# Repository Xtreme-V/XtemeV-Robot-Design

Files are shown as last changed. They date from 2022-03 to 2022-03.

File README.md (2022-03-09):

# XtemeV Robot
This robot was designed for the task given in **EN2532 - Robot Design and Competition** module in Semester 3 (2021), University of Moratuwa.

## Task
1. Line following
    - The robot must follow a white line on a black surface. These paths may contain straight
lines, curved lines, or dotted line segments.
2. Wall maze
    - After a line following section, the robot will have to navigate through a wall maze
section. This maze will not contain any looping paths. (A single possible path from
start to end is guaranteed.)
3. Mosaic Floor Area
    - The robot exiting the wall maze should immediately enter the mosaic floor area and
proceed to complete the following subtasks. Inserting the key solids to respective
keyholes to close the bridge. Collecting the ball of the color assigned to your team at
the start of the competition.
4. Bridge
    - The robot should cross the closed bridge and exit the area to a dotted line segment.
5. Shooting area
    - The robot must choose the correct path at the Y junction area according to the assigned color. While staying in the restricted space, the robot will have to shoot the
collected ball into the goal.
<br>
<p align="center">
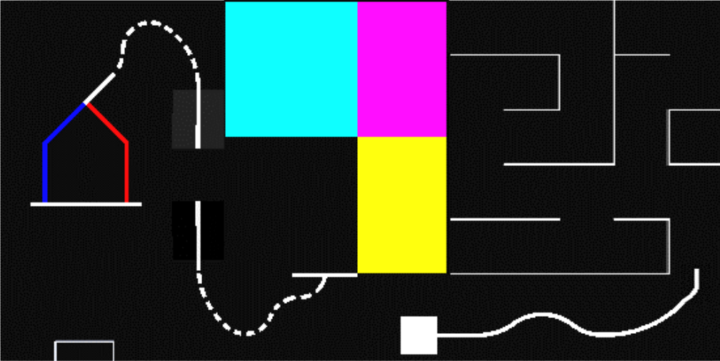
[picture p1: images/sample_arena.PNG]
    
</p>
<br>

## Robot Design
<br>
<p align="center">
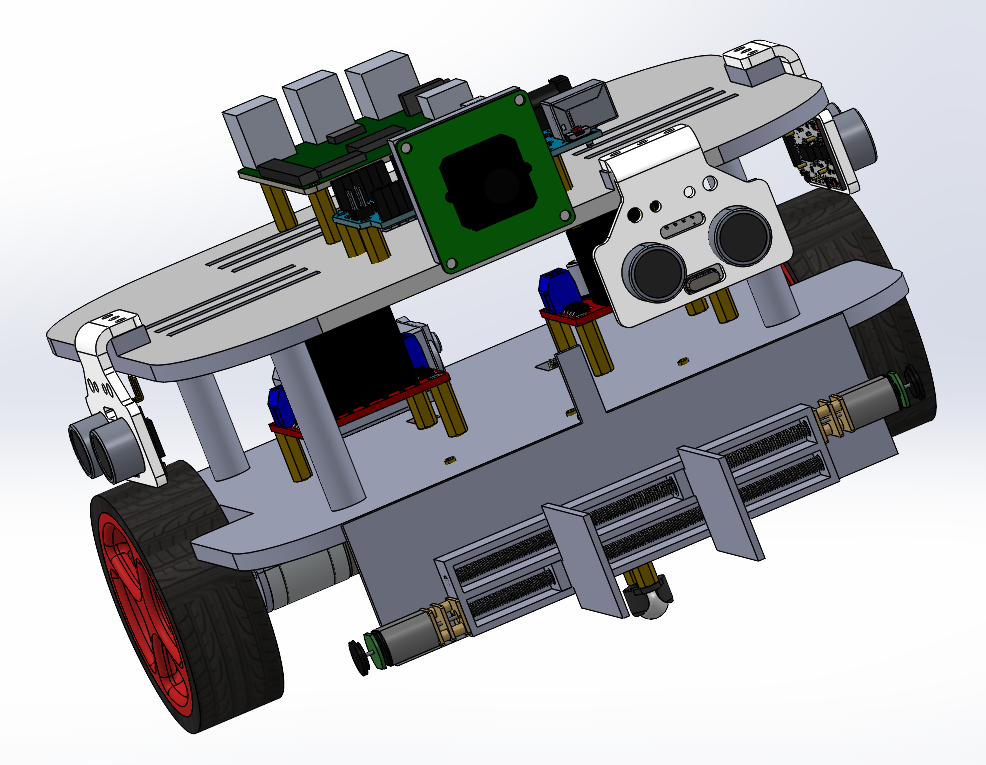
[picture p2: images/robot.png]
    
</p>
<br>

### Components that are being used in our robot are as follows,
- Pololu motors 
- N20 motors
- IR panel (QTR - 8RC)
- Ultrasonic Sensor (HC-SR04)
- Raspberry Pi Camera
- Raspberry Pi 3B+
- Arduino Mega
- Motor Controller (L298N)
## Team Members
- [K. D. Supun Dasantha Kuruppu](https://github.com/SupunDK)
- [W. M. Limalka Sadith](https://github.com/limalkasadith)
- [Sithuruwan Prathapasinghe](https://github.com/PrathapasingheSP99)
- [E. M. Dumindu Ashen Bandara](https://github.com/Dumindu-Bandara)
- [Biyon Fernando](https://github.com/BiyonFernando)

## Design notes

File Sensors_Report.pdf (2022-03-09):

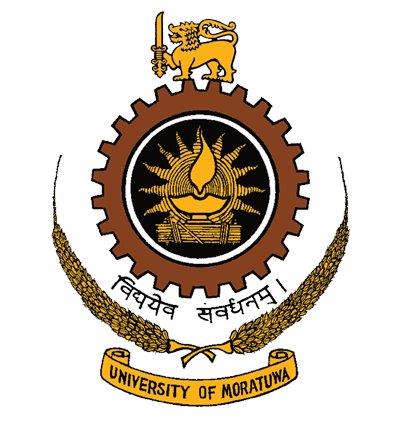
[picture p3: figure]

## Department of Electronic & Telecommunication Engineering

## University of Moratuwa

### Sensor Selection - XtremeV

14

## th October 2021

Bandara E. M. D. A. | 190072E
Fernando P. B. M. | 190178J
Kuruppu K. D. S. D. | 190338C
Prathapasinghe S. P. | 190470X
Sadith W. M. L. | 190538N

### 1. Motor Encoders

We are planning to use two types of motors in our robot. They are,

- DC Gear Motors
- Servo Motors

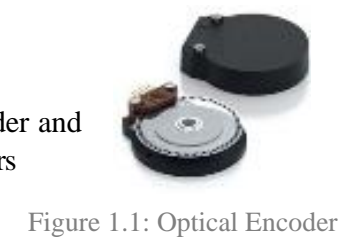
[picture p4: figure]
Figure 1.1: Optical Encoder

Since both the motors need to be controlled accurately, an optical quadrature encoder and an angle position tracking encoder is used in the DC Gear Motors and Servo Motors respectively.

Encoder for Servo Motor

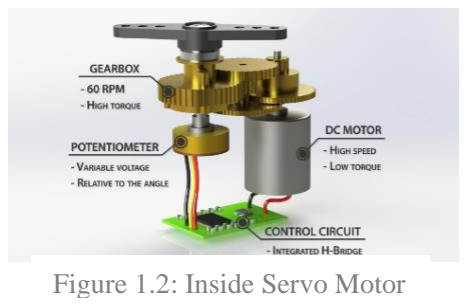
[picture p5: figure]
Figure 1.2: Inside Servo Motor

We are planning to use servo motors for the pick-and-place mechanism. It will require an angle position tracking encoder to control the angle of the servo motors. In the encoder market, we can purchase separate encoder modules which can connect to servo motors externally. The E3 optical kit encoder is an example for such an encoder. Since most of the servo motors have built-in potentiometer encoders, using such kind of servo motors for our robot is more economical. Therefore, we are planning to use Metal Wheel MG995 servo motors that have potentiometers as encoders.

Quadrature Encoder for Gear Motors

We chose the Pololu Gearmotor 25Dx64L which has a Hall effect Quadrature Encoder with a 1632 counts per revolution, as the wheel encoders for the DC Gear Motors. A high-resolution encoder was selected to achieve high controlling accuracy. The Quadrature Encoder is selected to fulfil the requirements for controlling the gear motors, which are to measure the rotational speed and the direction of the motor. The disadvantages of other encoder techniques are as follows,

Incremental Encoder (Not Quadrature) | It cannot measure the rotational direction of the motor
Absolute Encoder | The additional feature of precisely measuring the rotated angle is not required for our application

Even though optical encoders offer higher accuracy compared to magnetic
encoders in clean, and quiet environments, their performance significantly drop in environments with oil, dirt, and moisture. Similarly, their performance is affected by shock and vibration as well. On the contrary, the Hall effect encoders copes very well with shock and vibration while being unaffected by the ingress of oil, dirt, and moisture. Moreover, the hall effect encoders are compact and cost-effective, which makes them ideal for our application.

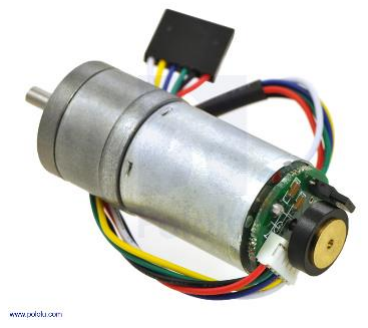
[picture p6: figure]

Figure 1.3: Pololu Gear motor

### 2. Distance Sensor

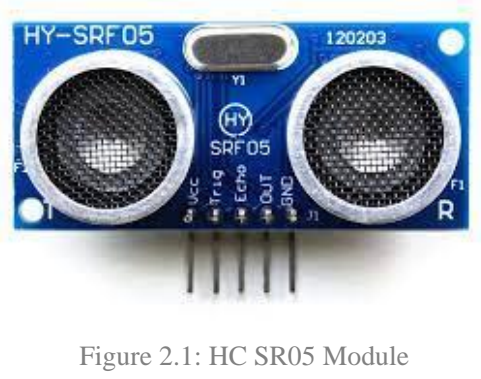
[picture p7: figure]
Figure 2.1: HC SR05 Module

HC-SR05 ultrasonic sensor has been chosen as the distance sensor for the maze navigation task in our robot. Three sensors are mounted on top of the robot to identify the obstacles around it. Ultrasonic sensors use the concept of time of flight to calculate the distance to an obstacle. It measures the time between transmitted and received signal and calculate distance using speed of sound in the air. There are two popular sensors in the ultrasonic sensor category. The HC-SR05 has been chosen over HC-SR04 due to its higher precision and the availability of the 3-pin mode operation. HC-SR05 sensor equipped with five pins, one each for VCC, Trigger, Echo, Out and Ground. It has a measurement range of 2cm to 450cm. One drawback of ultrasonic sensor is that its transmitted signals get distorted around complex objects.

Following is a comparison between alternatives available for ultrasonic sensors.

Ultrasonic | Sharp-IR | LIDAR | VCSEL
Low range | Low range | High range | Low range
Low frequency data retrieval | Low frequency data retrieval | High frequency data retrieval | High frequency data retrieval
Less Cost | Moderate Cost | High Cost | High Cost
Multiple interface options | Analog output | UART/ I2C | I2C interface only
Low resolution | High resolution | High resolution | High resolution

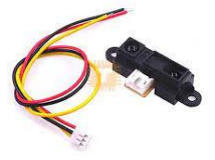
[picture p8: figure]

### 3. IR Sensor Array

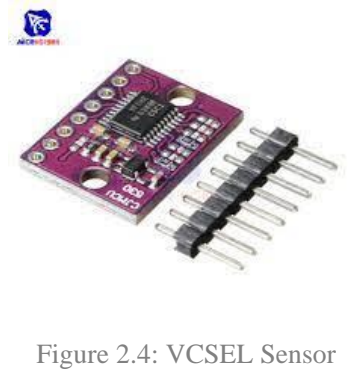
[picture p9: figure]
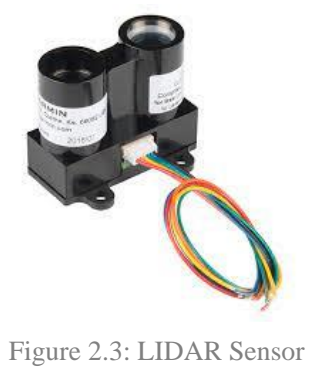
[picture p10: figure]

In this device, there are several IR sensors connected in series. There can be 5 sensors, 7 sensors or 8 sensors. This device used for the line following task. It’s easy to place and drive the robot in the middle of the line with this array.

Suitable IR Sensor arrays for the project are,

Figure 2.2: Sharp IR | Figure 2.3: LIDAR Sensor | Figure 2.4: VCSEL Sensor

Table 2.1: Comparison between distance sensors

1. Pololu QTR 8-bit Line Hunter Sensor Array Module for Arduino (MD0601) This IR array has 8 TCRT5000 IR sensors. It is a good sensor for line-following robots. It is very precise and easy to handle as well. The sensor outputs are digital I/O-compatible signals that can be read as a timed high
pulse. Moreover, there are LEDs for each sensor for indication. Operating voltage: - 3.3V - 5V Operating current: - 100mA Price: - Rs.2950.00

### 2. Reflective Sensor Array Raykha S8

This is the local version of the above sensor array. It is made in Sri Lanka, and it is as good as Pololu IR sensors but not that expensive. Each IR sensor has its own Digital I/O measurable output, variable analogue voltage output and an LED for indication purposes.
Supply Voltage: - 5V
Supply current: - max 200mA Price: - Rs.1290.00

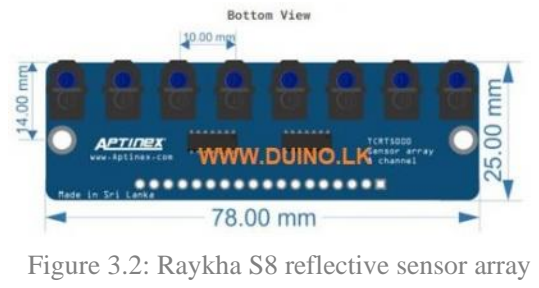
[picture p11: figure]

Comparison between Pololu and Rekha IR sensor arrays are as follows,

Pololu IR array | Rekha IR array
Expensive | Cheaper than Pololu
Have a built-in library | Don’t have built-in libraries

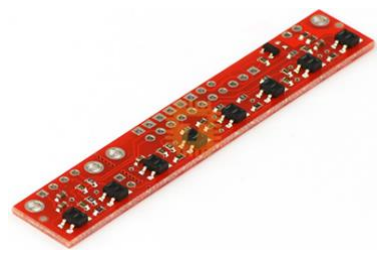
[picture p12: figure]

More precise values | Accuracy is a bit lower than Pololu
Both can give digital as well as analog outputs

### 4. IR Array or Camera

We are planning to use the camera for colour detection, object detection and obstacle detection. We have an idea to use the same camera module to accomplish the line following task as well. However, since we are unsure about the suitability of that approach, we are planning to experiment and decide. If it works, we won’t need an IR array for the line following task. Therefore, it would decrease the budget of the project.

Camera Module Selection

We planned to do following tasks using the Raspberry Pi camera,

1. Dotted Line Following
2. Object Detection
3. Colour Detection

Available Camera modules

### 1. Raspberry Pi Camera V2.1 (Original) (8MP)

Capture Resolution: 1080p
Special Feature: Time Lapse Price: Rs.6250.00

Figure 3.1: Pololu QTR IR Module

Figure 3.2: Raykha S8 reflective sensor array

Figure 4.1: Raspberry Pi Camera V2.1

Figure 4.2: Banana Pi Camera Module

Table 3.1: Comparison between Pololu and Rekha IR sensor arrays

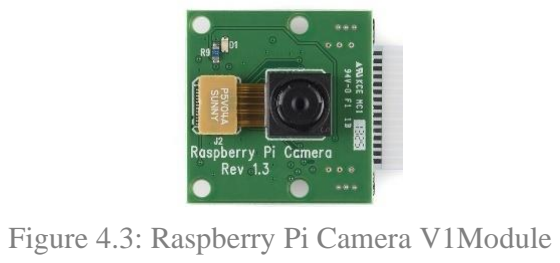
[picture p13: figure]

### 2. Banana Pi Camera Module (5MP)

Capture Resolution: 1080p
Price: Rs.5500.00

### 3. Raspberry Pi Camera V1 (5MP)

Capture Resolution: 1080p
Price: Rs.1490.00

### 4. Raspberry Pi NoIR Camera Module V2 (8MP)

Official Night vision camera for RPi Capture Resolution: 1080p
Special Feature: Time Lapse, Night Vision Price: Rs.7250.00

We decided to use Raspberry Pi Camera V1 (5MP) module because its cost effective and capable of performing all the desired tasks. Since we are planning to use the Raspberry Pi camera in multiple occasions, native compatibility with the Raspberry Pi board is a huge advantage and it would allow efficient use of board’s resources. Furthermore, the availability of this camera module in the local market (Tronic.lk) is another advantage.

### 5. References

1. https://www.seeedstudio.com/blog/2020/05/14/raspberry-pi-camera-comparison-of-high-quality-camera-with-camera-module-v2/ (https://www.seeedstudio.com/blog/2020/05/14/raspberry-pi-camera-comparison-of-high-quality-camera-with-camera-module-v2/)
2. https://tronic.lk/product/banana-pi-camera-module
3. https://tronic.lk/product/raspberry-pi-noir-camera-v2-sony-imx219-sensor-8-megapi
4. https://tronic.lk/product/raspberry-pi-camera-v2-1-sony-imx219-sensor-8-megapixel
5. https://www.amazon.com/Raspberry-Pi-Camera-Module-Megapixel/dp/B01ER2SKFS
6. https://maker.pro/raspberry-pi/projects/raspberry-pi-webcam-robot
7. https://forums.raspberrypi.com/viewtopic.php?t=42169
8. https://www.sparkfun.com/distance_sensor_comparison_guide
9. https://www.seeedstudio.com/blog/2019/12/23/distance-sensors-types-and-selection-guide/

Figure 4.3: Raspberry Pi Camera V1Module

Figure 4.3 Raspberry Pi NoIR Camera Module

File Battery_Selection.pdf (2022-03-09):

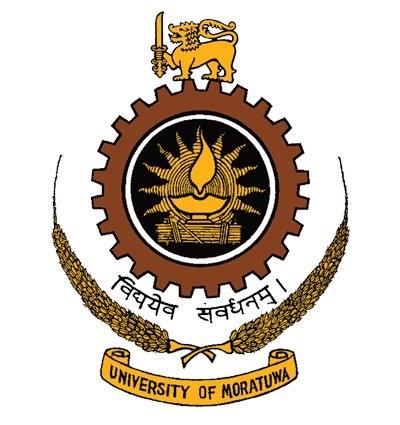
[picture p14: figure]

### Department of Electronic & Telecommunication Engineering

### University of Moratuwa

Assignment – 8

EN2532 - Robot Design and Competition

Bandara E. M. D. A. | 190072E
Fernando P. B. M. | 190178J
Kuruppu K. D. S. D. | 190338C
Prathapasinghe S. P. | 190470X
Sadith W. M. L. | 190538N

### 19th November 2021

Power Budget Calculation

The current and voltage requirements of the components that are being used in our robot are as follows,

Component | Quantity | Voltage | Operating Current | Maximum Current
Pololu motor | 2 | 6 V | 2.06 A (1.03 A x 2) | 5.6 A (2.8 A x 2)
N20 motor | 2 | 6 V | 2 A (1 A x 2) | 3 A (1.5 A x 2)
IR panel | 1 | 5 V | 100 mA | 100 mA
Ultrasonic Sensor | 3 | 5 V | 45 mA (15 mA x 3) | 45 mA (15 mA x 3)
Raspberry Pi 3B+ | 1 | 5 V | 3 A | 3 A
Solenoid | 1 | 12 V | 350 mA | 350 mA
Arduino Uno | 1 | 5 V | 200 mA | 200 mA
Motor Controller | 2 | 5 V | 80 mA (40 mA x 2) | 80 mA (40 mA x 2)
Total | | | 7.835 A | 12.375 A

Voltage

The component that requires the maximum voltage in the component list is the Solenoid. It requires 12 V, and all the other components require 6 V or less. Furthermore, the Solenoid only requires 350 mA which is relatively low. Therefore, we decided to use a boost converter along with a 11.1 V battery for our robot.

Capacity

The maximum current draw and the operating current draw of the robot are 12.375 A and 7.835 A respectively. Since the maximum current draw only occurs when the DC motors are in the stall condition, considering a continuous current draw of 12.375 A is not realistic. Therefore, the capacity requirement for the robot is based on the operating current. Furthermore, we decided that a 20-minute continuous run-time for the robot is sufficient for our application. Therefore, the required capacity of the power source is calculated as follows,

Capacity = CurrentDraw(mA) ∗ Time(ℎours)

Capacity = 7835 ∗ (

20
60)

Capacity = 2611 mAℎ

Discharging Rate

The capacity of the required battery is 2611 mAh. The operating current of the robot is 7.835
A. Therefore, the required discharging rate should be greater than,

Discℎaring Rate =

7835
2611

Discℎaring Rate = 3 C

The summarised requirements of the power source are as follows,

Voltage | Capacity | Discharging Rate
11.1 V | 2611 mAh | 3C or above

Battery Selection

The NiCd battery is not considered as a viable battery option due to the toxic nature of the battery and the memory effect associated with its rechargeability.

The Lead Acid battery is also not considered as a viable battery option, since it is considerably heavy, and it is not suitable for a compact mobile robot as ours.

| Alkaline | NiMH | LiPo | Li-ion
Capacity | Low | High | High | High
Discharging Rate | Low | Low | High | Low
Power Density | Low | Moderate | High | High
Rechargeability | Not Available | Available | Available | Available

Since we require a rechargeable battery with high capacity and discharging rate, we identified the LiPo battery as the most suitable based on the above comparison table.

The following LiPo battery in the market fulfils all the identified requirements.

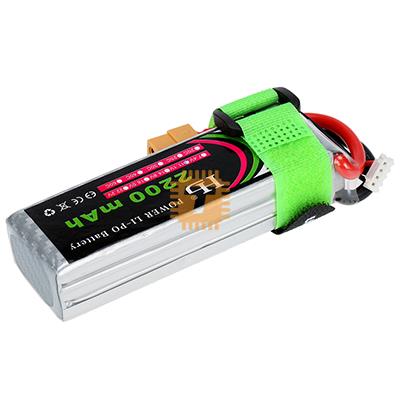
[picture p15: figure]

https://tronic.lk/product/11-1v-2200mah-3s-25c-lipo-battery-xt60-plug

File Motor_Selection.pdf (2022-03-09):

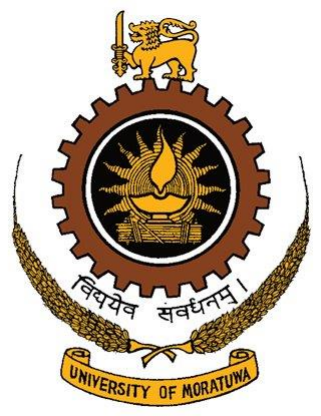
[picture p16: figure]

### Department of Electronic & Telecommunication Engineering

### University of Moratuwa

Assignment – 5

EN2532 - Robot Design and Competition

27

### th October 2021

Bandara E. M. D. A. | 190072E
Fernando P. B. M. | 190178J
Kuruppu K. D. S. D. | 190338C
Prathapasinghe S. P. | 190470X
Sadith W. M. L. | 190538N

Robot Weight Calculation

The list of chosen components that add a significant weight to the robot are as follows,

- Battery: 250 g
- Raspberry-Pi 3B+ with clear case: 64 g
- MG995 Servo Motor (x2): 110 g
- Gripper: 100 g
- Robot Chassis with wheels: 330 g
- Motor Driver: 26 g
- Motor (x2): 202 g
- Caster Wheel (x2): 80 g

Therefore, the total weight of the robot accounts to,

Total weight = 1162 g

Requirements

1. Qualitative Requirements
- Since this robot is made for the EN2532 module, we only require the robot to last for six months.
- The motor should be affordable to align with the budget of the project.
- Medium level of accuracy is sufficient for the application.
2. Quantitative Requirements
- The distance the robot needs to traverse was estimated to be 20 m. We intend to complete the task within 5 minutes. Therefore, we chose the maximum velocity of the robot as 11 cms

-1
- The motors need to be able to provide enough torque to propel a weight of 1119 g on a 20° slope.
- The motor should run at 30% of its stall torque to operate with low current draw to ensure minimize losses.

Considering the above qualitative requirements, the Brushed DC motor seems the most suitable motor type for our application. Therefore, the following calculations are done in order to determine the quantitative requirements for the Brushed DC motors.

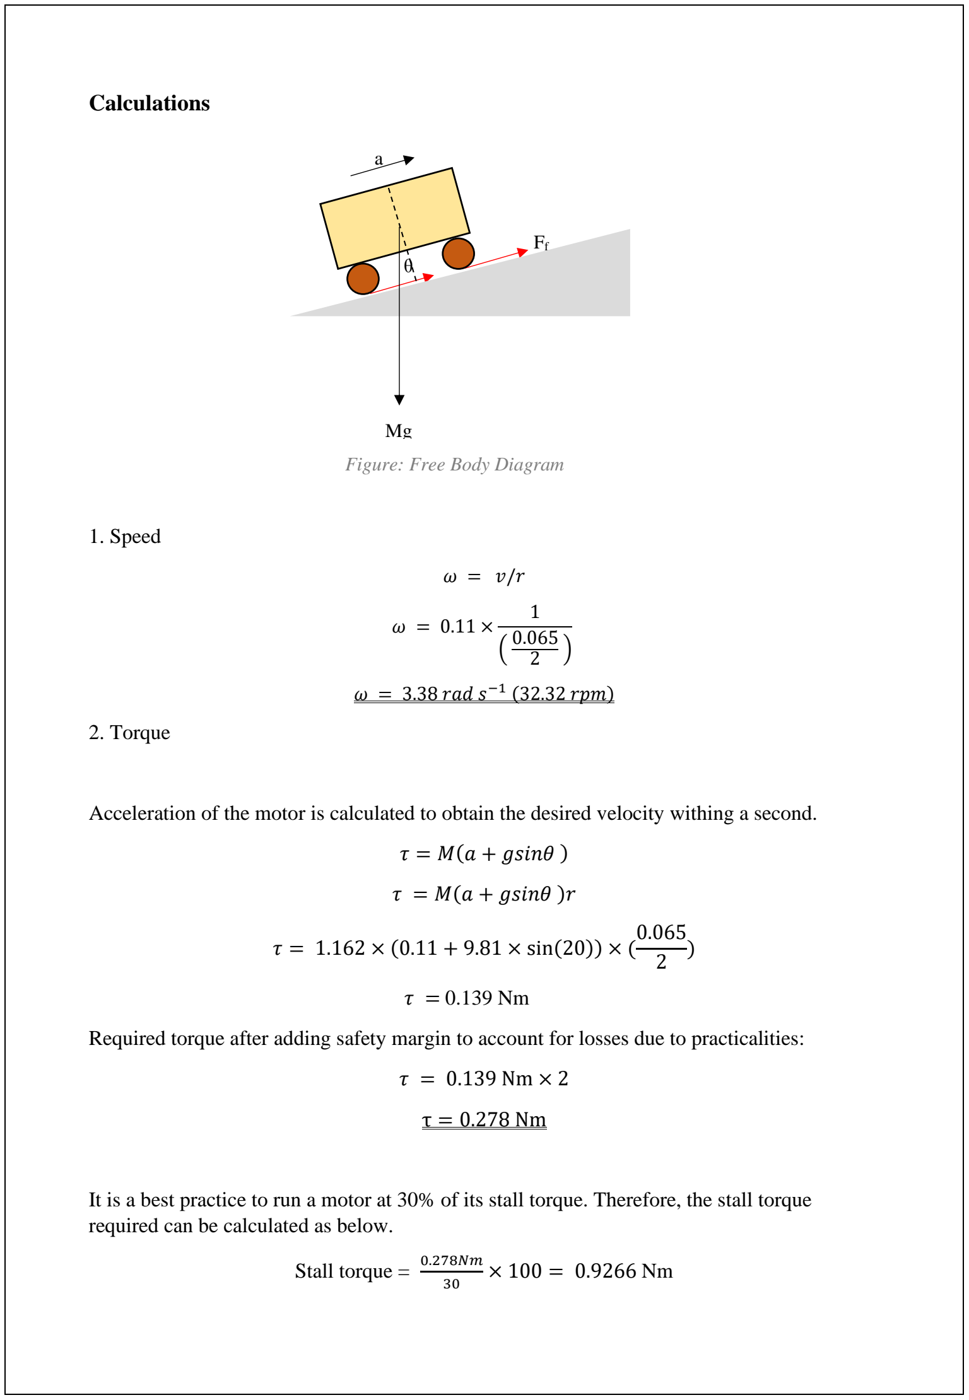
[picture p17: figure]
Calculations; 1. Speed; ω = 3.38 rad s; (32.32 rpm); 2. Torque; τ = M(a + gsinθ ); τ = M(a + gsinθ )r; τ = 1.162 × (0.11 + 9.81 × sin(20)) × (; required can be calculated as below.; Stall torque =; Figure: Free Body Diagram

Acceleration of the motor is calculated to obtain the desired velocity withing a second.

Required torque after adding safety margin to account for losses due to practicalities:

It is a best practice to run a motor at 30% of its stall torque. Therefore, the stall torque

Required Specifications for the DC motor

Motor type | Brushed DC Motor
Operational toque | 0.278 Nm (39.368 oz.in)
Operational speed | 3.38 rad s⁻¹ (32.32 rpm)
Stall torque | 0.9266Nm (131.22 oz.in)

Specifications of suitable DC motors

34:1 Metal Gearmotor 25Dx64L mm HP 12V with 48 CPR Encoder (No End Cap)
No Load RPM | 290 rpm
Stall torque | 120 oz-in

The above motor has a stall torque of 120 oz-in which is close to the required value of 131.22 oz-in. Furthermore, the No Load RPM is 290 rpm. Therefore, this motor aligns with all the boundary requirements.

According to the torque speed graph, we can calculate the operational speed at our required torque.

Operational speed = (

290
120

) × (120 − 39.368 ) = 194.86 rpm

The above calculation indicate that the motor can accommodate the required operational speed at the operational torque.

34:1 Metal Gearmotor 25Dx52L mm HP 12V
No Load RPM | 300 rpm
Stall torque | 150 oz-in

The above motor has a stall torque of 150 oz-in which is greater than 120 oz-in. The No Load RPM of the motor is 300 rpm which can easily accommodate our requirements.

According to the torque speed graph, we can calculate the operational speed at our required torque.

Operational speed = (

300
150) × (150 − 39.368 ) = 221.26 rpm

The above calculation indicate that the motor can accommodate the required operational speed at the operational torque.

Conclusion

After considering the above calculations and the qualitative requirements, we have selected 34:1 Metal Gearmotor 25Dx64L mm HP 12V with 48 CPR Encoder (No End Cap) as it is both suitable for our application and provided by the university.

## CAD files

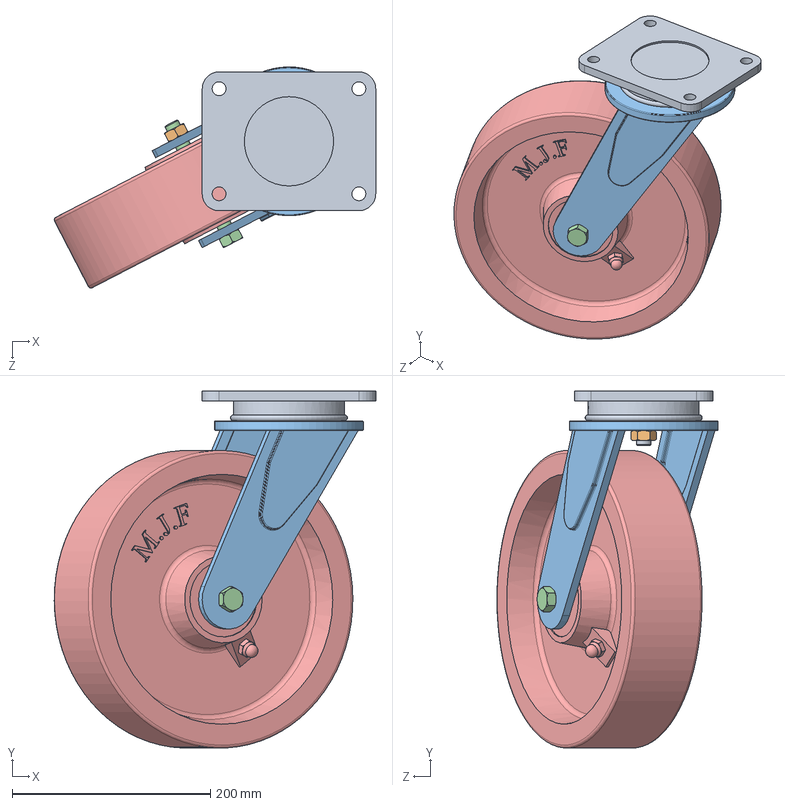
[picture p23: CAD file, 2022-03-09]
3D Design/Other parts/assembly of caster wheel.SLDASM
324.2 x 359.9 x 223.0 mm
part 1 mounting plate
part 2 nut x 2
part 3 horn
part 4 bolt
part 5 wheel

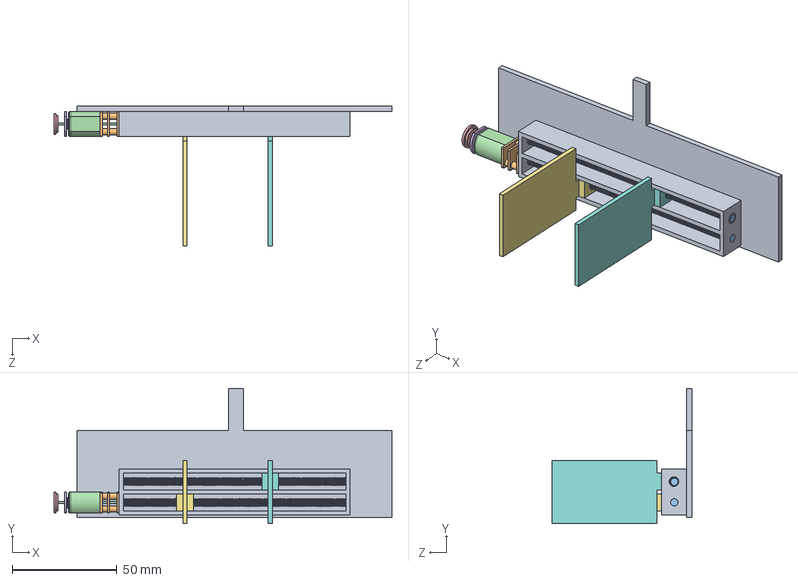
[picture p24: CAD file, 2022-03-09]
3D Design/gripper/Assem1.SLDASM
161.0 x 64.4 x 66.5 mm
rail
threaded rod.step x 4
handleft
handrigt

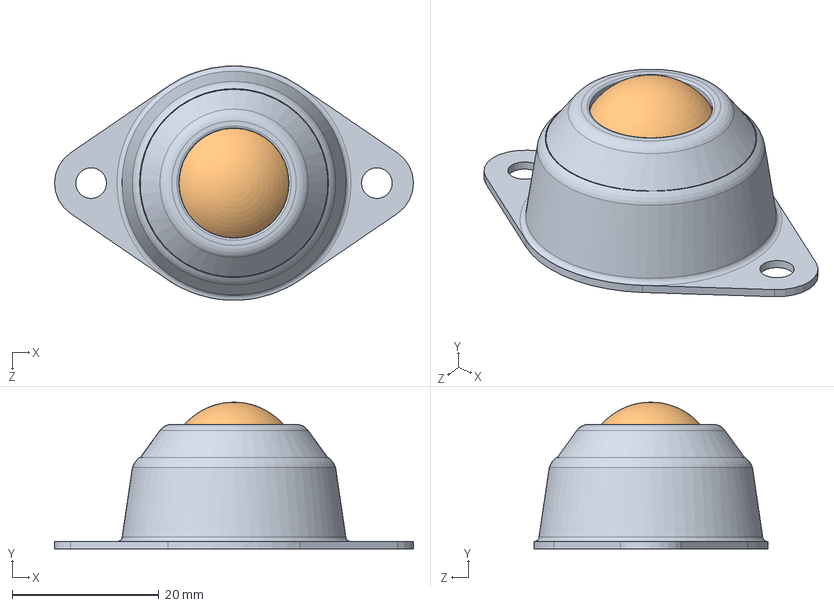
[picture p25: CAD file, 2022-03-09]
3D Design/Other parts/3/Omni wheel steel ball OW007.SLDASM
49.0 x 20.0 x 32.0 mm
Base
Balle
Fond

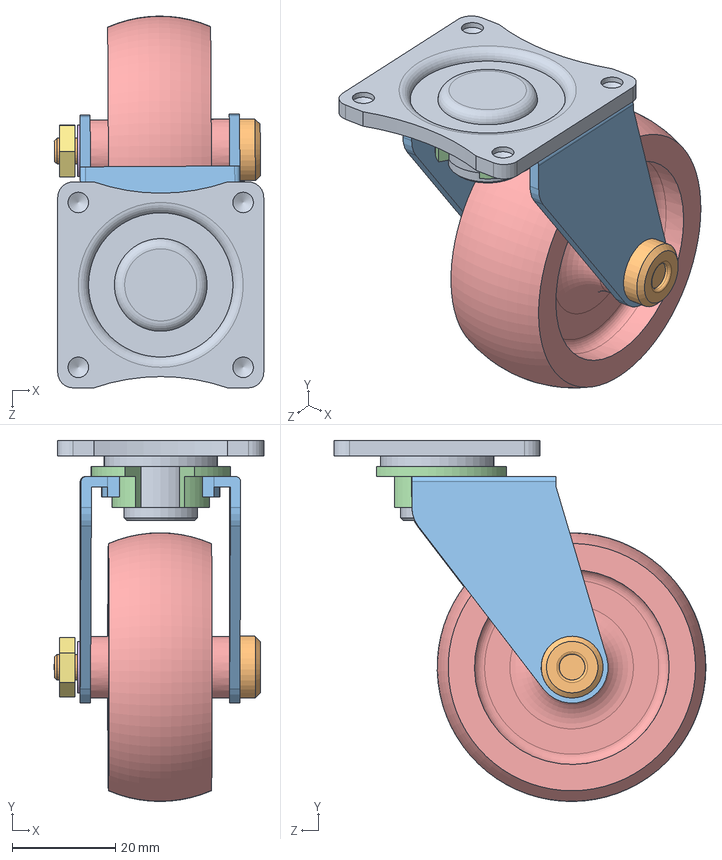
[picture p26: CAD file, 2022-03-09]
3D Design/Other parts/Castor Wheel Assembly.SLDASM
40.7 x 70.1 x 72.2 mm
Top
Holder
HOLDER 2
bottom
Wheel
washer
Nut

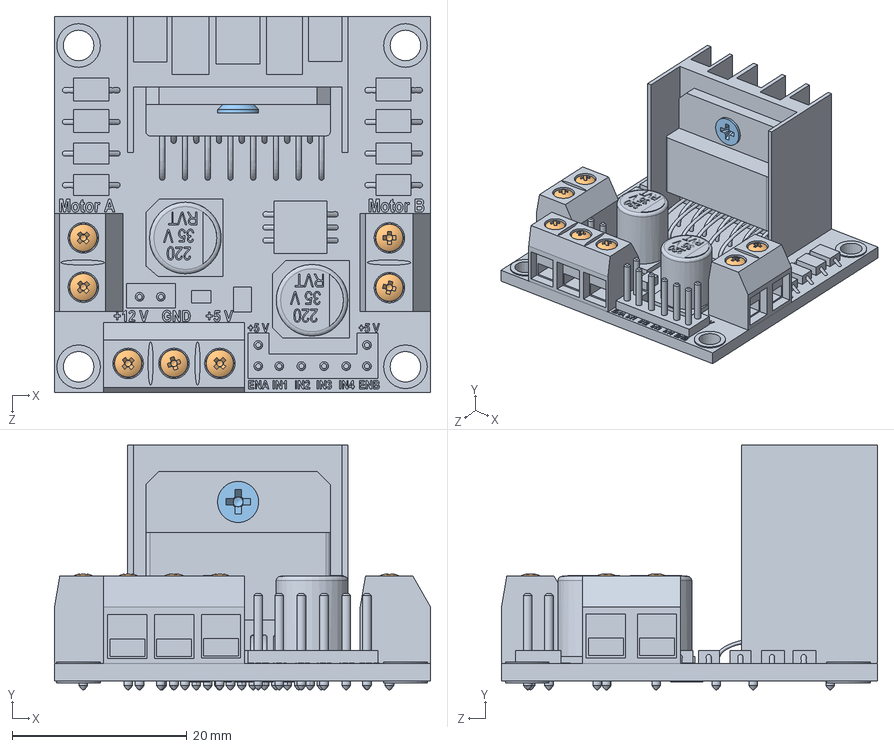
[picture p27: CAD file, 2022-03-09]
3D Design/Other parts/L298N Stepper Motor Driver Assembly.SLDASM
43.0 x 28.0 x 43.0 mm
L298N Stepper Motor Driver (Red)-Part File
pan head cross recess screw_iso_ISO 7045 - M1.6 x 4 - Z - 4N x 7
countersunk flat head cross recess screw_iso_ISO 7046-1 - M2.5 x 3 - Z - 3N

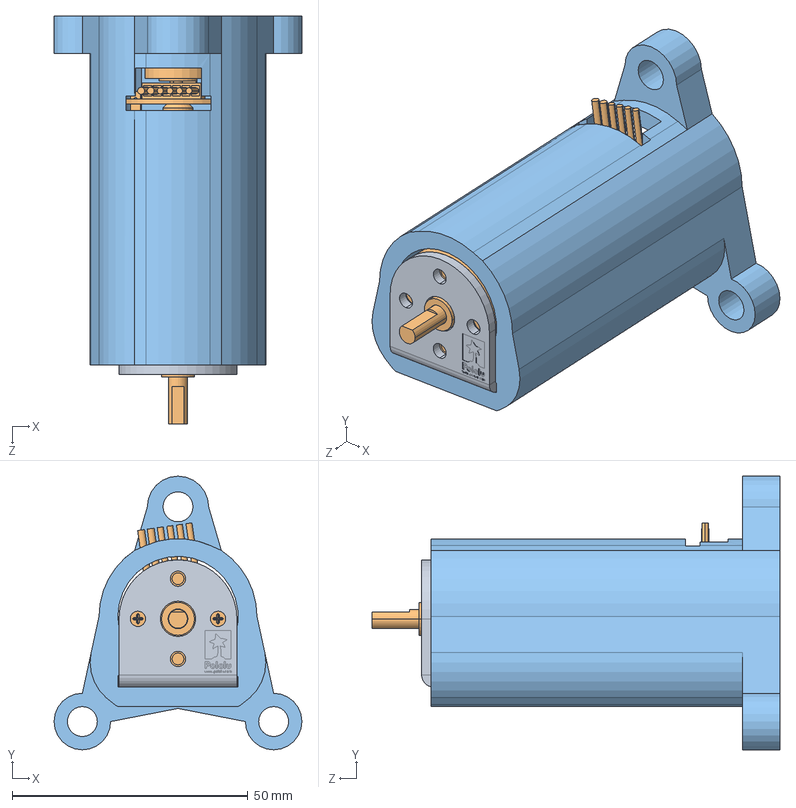
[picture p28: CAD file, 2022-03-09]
3D Design/Other parts/MotorenSoporte.SLDASM
52.6 x 58.0 x 86.5 mm
pololu-25d-mm-metal-gearmotor-bracket
25D-metal-gearmotor-75-encoder
SoporteMotor

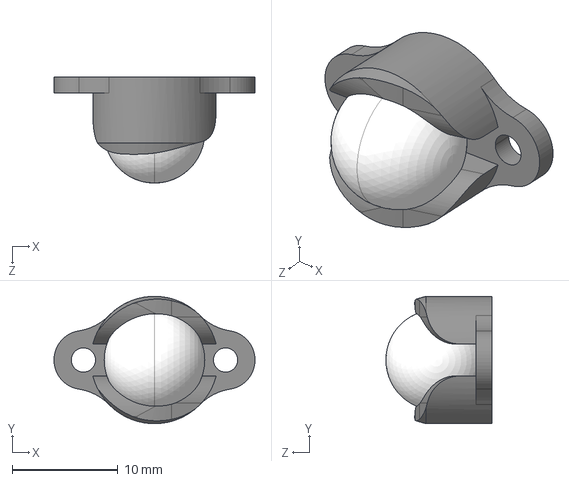
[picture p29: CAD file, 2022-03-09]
3D Design/gripper/casterwheel/pololu-ball-caster-with-0-375in-ball.step
19.0 x 12.1 x 10.1 mm

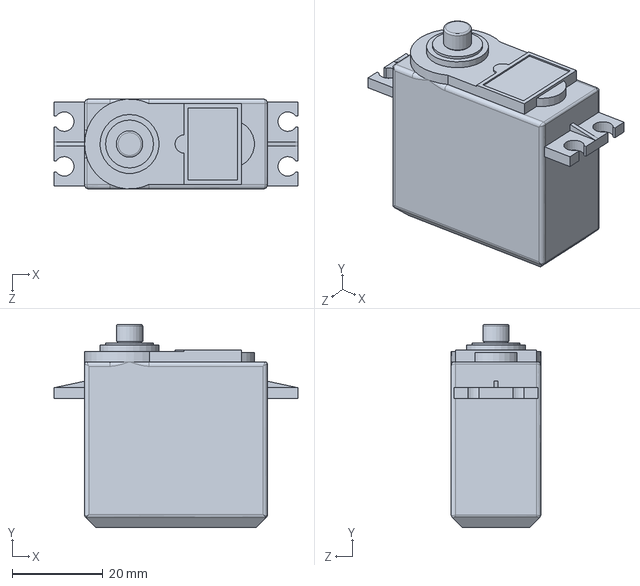
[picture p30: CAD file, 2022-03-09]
3D Design/gripper/kiso.SLDPRT
53.8 x 44.8 x 19.8 mm

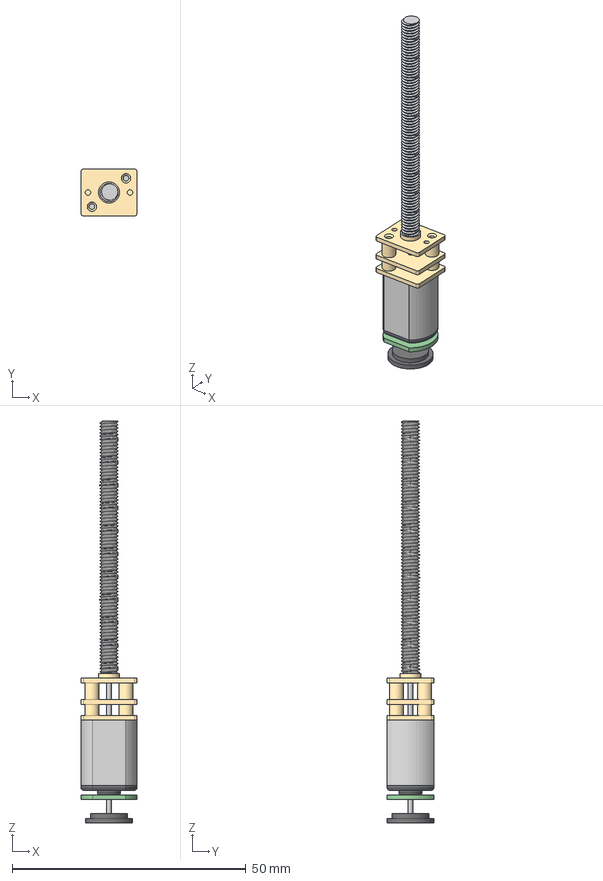
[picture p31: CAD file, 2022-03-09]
3D Design/gripper/motor/n20 m4x55 encoder v2.step
12.0 x 10.0 x 86.0 mm
gearbox
threaded rod
n20 motor
magnet
encoder

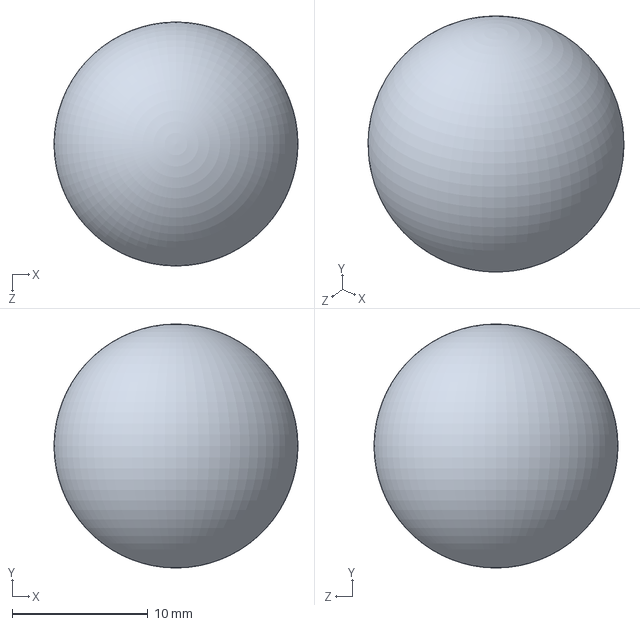
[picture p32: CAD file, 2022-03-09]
3D Design/Other parts/3/Balle.SLDPRT
18.0 x 18.0 x 18.0 mm

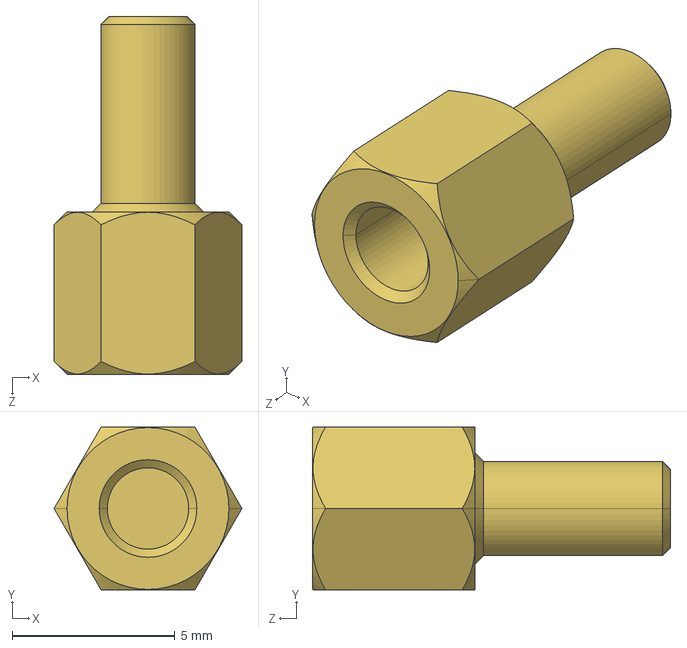
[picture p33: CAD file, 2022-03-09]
3D Design/Other parts/m3-standoff-pcb-spacers-1.snapshot.2/M3_M_TO_F_5MM_STANDOFF.STEP
5.77 x 5.00 x 11.0 mm

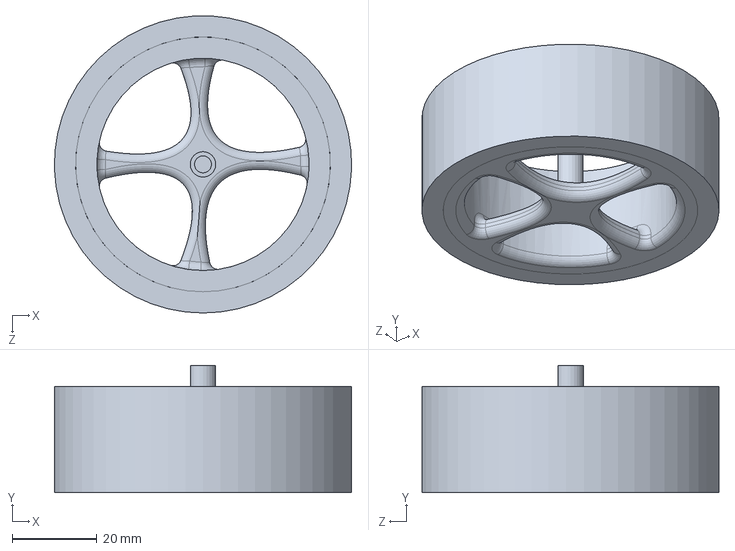
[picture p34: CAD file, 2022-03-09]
3D Design/Other parts/wheel - 1/wheel.SLDPRT
70.0 x 30.0 x 69.9 mm

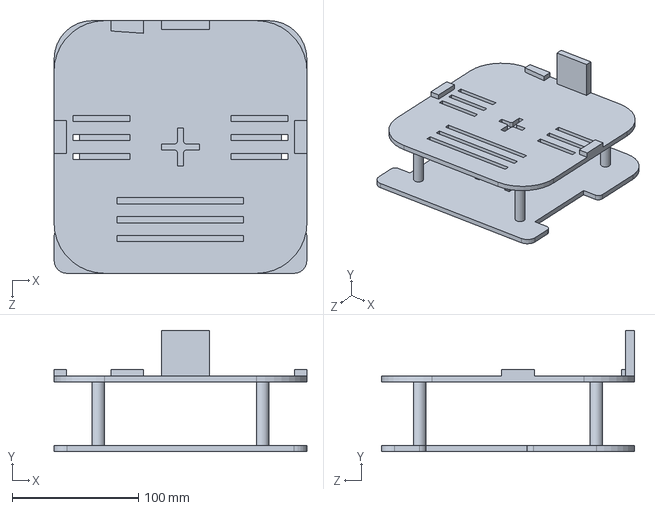
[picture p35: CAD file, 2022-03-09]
3D Design/robot chassis.SLDPRT
200.3 x 96.0 x 200.0 mm

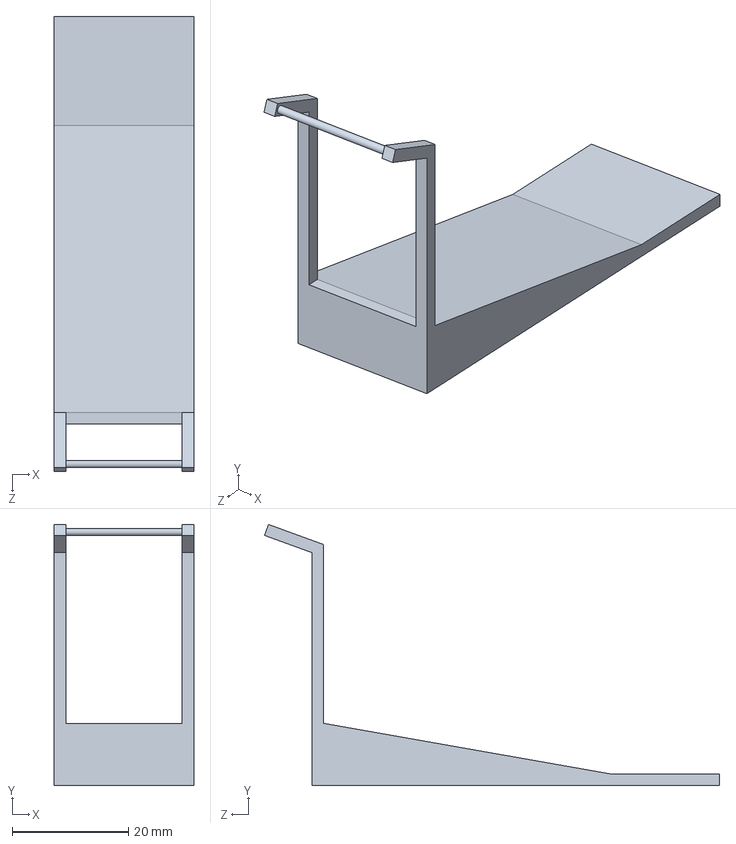
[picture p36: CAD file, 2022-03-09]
3D Design/solenoid/connector.SLDPRT
24.0 x 44.9 x 78.2 mm

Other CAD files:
3D Design/gripper/hand.SLDPRT
3D Design/Other parts/25D-metal-gearmotor-75-encoder.SLDPRT
3D Design/Other parts/3/Fond.SLDPRT
3D Design/Other parts/m3-standoff-pcb-spacers-1.snapshot.2/M3_F_TO_F_10MM_STANDOFF.STEP
3D Design/Other parts/3/Base.SLDPRT
3D Design/Other parts/3/Omni wheel steel ball OW007.IGS
3D Design/Other parts/Hex Spacer MF M3 L35mm.stp
3D Design/Other parts/Innomaker_OV9281.stp
3D Design/Other parts/Raspberry pi 3B+ simplified.SLDPRT
3D Design/Other parts/SoporteMotor.SLDPRT
3D Design/Other parts/m3-standoff-pcb-spacers-1.snapshot.2/M3_F_TO_F_15MM_STANDOFF.STEP
3D Design/Other parts/m3-standoff-pcb-spacers-1.snapshot.2/M3_F_TO_F_20MM_STANDOFF.STEP
3D Design/Other parts/m3-standoff-pcb-spacers-1.snapshot.2/M3_F_TO_F_5MM_STANDOFF.STEP
3D Design/Other parts/m3-standoff-pcb-spacers-1.snapshot.2/M3_F_TO_F_STANDOFF.SLDPRT
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

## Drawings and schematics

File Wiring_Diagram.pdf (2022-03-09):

## SONAR1

# ULTRASONIC SENSOR +5V Trigger Echo Gnd

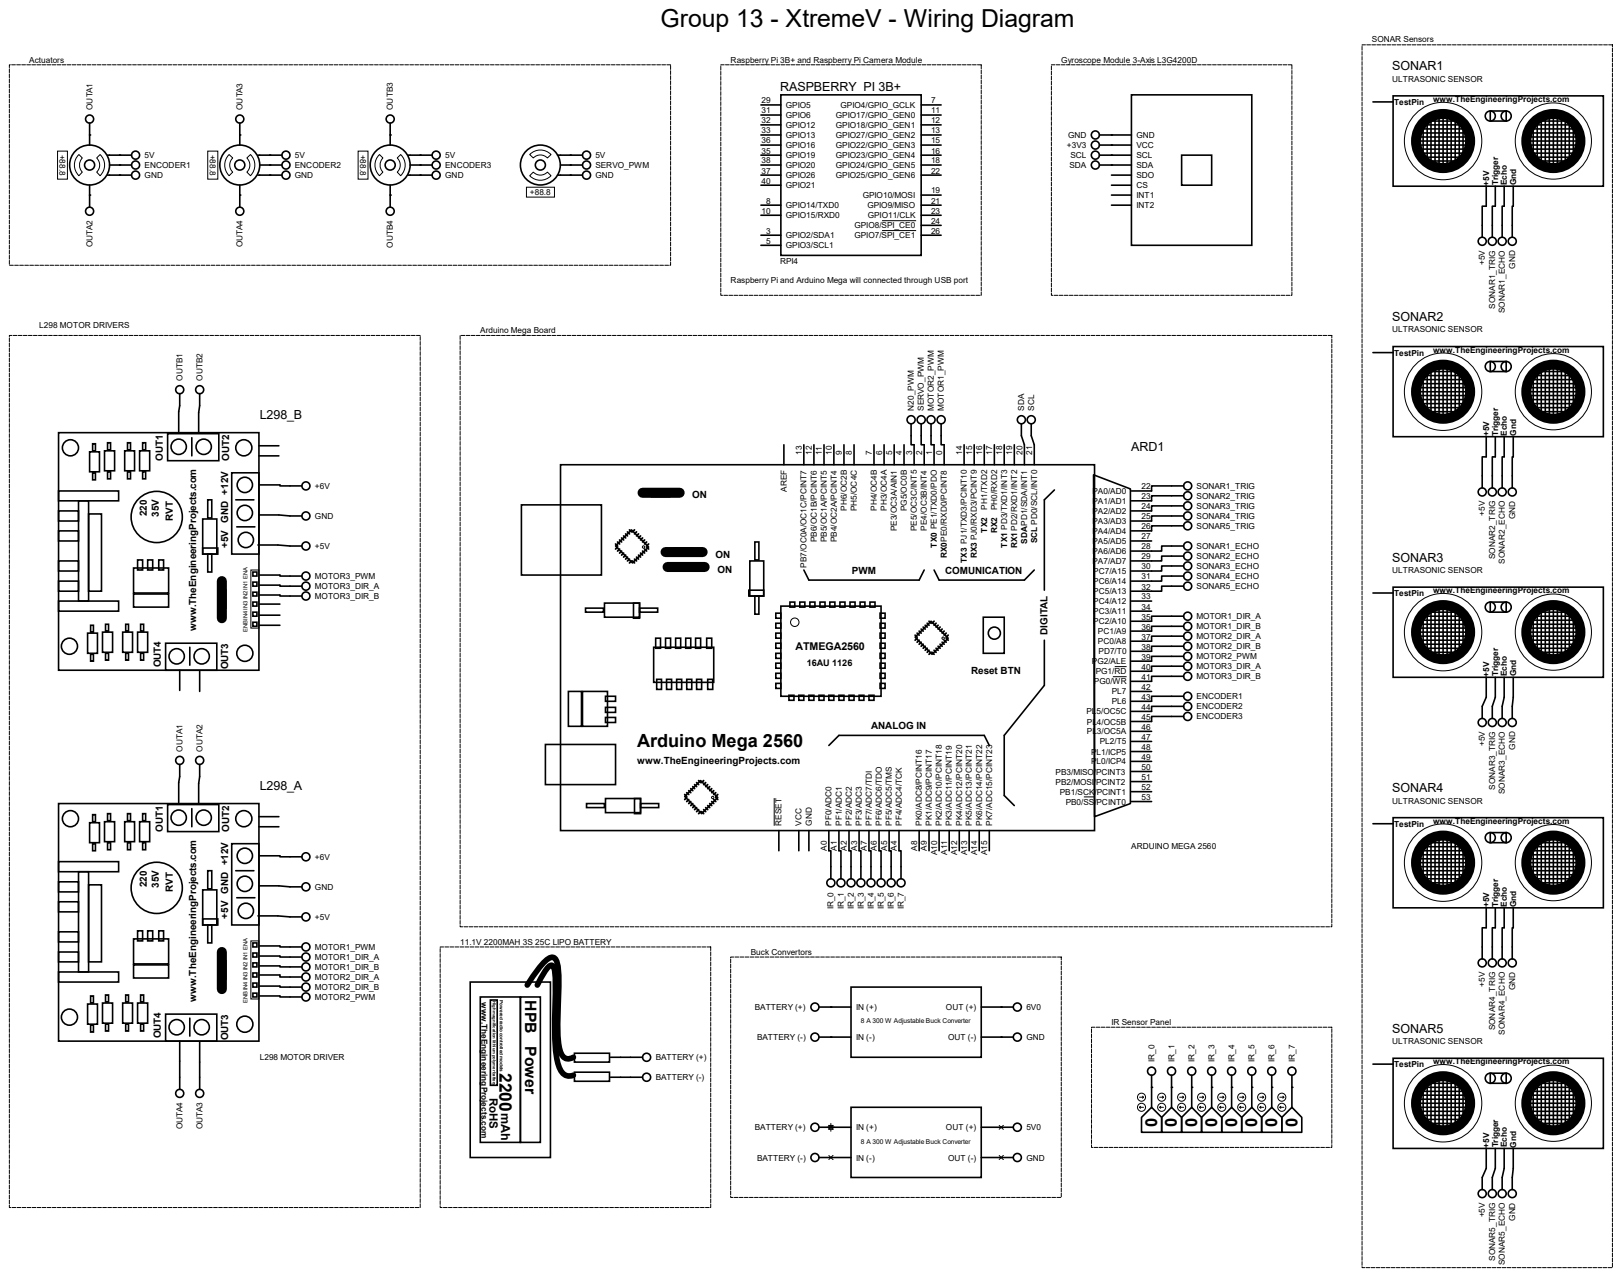
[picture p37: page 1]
PWM; COMUNICATION; DIGITAL; ANALOG IN; ATMEGA2560; TX⁰; TX³; TX²; TX¹; SDA SCL RX⁰; RX³; RX²; RX¹; Reset BTN; Arduino Mega 2560; PD⁰/SCL/INT0 21 PD¹/SDA/INT1 20 PD²/RXD¹/INT2 19 PD³/TXD¹/INT3 18 PH⁰/RXD² ¹⁷ PH¹/TXD² ¹⁶ PJ0/RXD³/PCINT9 15 PJ1/TXD³/PCINT10 14 PE⁰/RXD⁰/PCINT8; 0 PE1/TXD0/PDO; 1 PE4/OC3B/INT4; 2 PE5/OC3C/INT5; 4 PE3/OC3A/AIN1; PG2/ALE; PL1/ICP5; PL0/ICP4; PB3/MISO/PCINT3; PB2/MOSI/PCINT2; PB1/SCK/PCINT1; PB0/SS/PCINT0; ARD1; ARDUINO MEGA 2560; +5V Trigger Echo Gnd; SONAR2; SONAR3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

Group 13 - XtremeV - Wiring Diagram

SONAR Sensors
ULTRASONIC SENSOR +5V SONAR⁴_TRIG SONAR⁴_ECHO GND ⁺⁵V SONAR²_TRIG SONAR²_ECHO GND ⁺⁵V SONAR¹_TRIG SONAR¹_ECHO GND +5V SONAR³_TRIG SONAR³_ECHO GND +5V Trigger Echo Gnd
ULTRASONIC SENSOR +5V Trigger Echo Gnd

Raspberry Pi 3B+ and Raspberry Pi Camera Module

Gyroscope Module 3-Axis L3G4200D

TestPin www.TheEngineeringProjects.com

Raspberry Pi and Arduino Mega will connected through USB port

9 PB4/OC2A/PCINT4 10 PB5/OC1A/PCINT5 11 PB6/OC1B/PCINT6 12 PB7/OC0A/OC1C/PCINT7 13 AREF PK7/ADC15/PCINT23 A15 PK6/ADC14/PCINT22 A14 PK5/ADC13/PCINT21 A13 PK4/ADC12/PCINT20 A12 PK3/ADC11/PCINT19 A11 PK2/ADC10/PCINT18 A10 PK1/ADC9/PCINT17 A9 PK0/ADC8/PCINT16 A8 PF7/ADC7/TDI A7 PF6/ADC6/TDO A6 PF5/ADC5/TMS A5 PF4/ADC4/TCK A4 PF3/ADC3 A3 PF2/ADC2 A2 PF1/ADC1 A1 PF0/ADC0 A0 RESET VCC GND

www.TheEngineeringProjects.com

8 A 300 W Adjustable Buck Converter

IR Sensor Panel IR_0

SONAR5
ULTRASONIC SENSOR +5V SONAR⁵_TRIG SONAR⁵_ECHO GND

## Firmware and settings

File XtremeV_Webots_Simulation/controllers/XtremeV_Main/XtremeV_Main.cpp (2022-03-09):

// XtremeV_controller
#include "MainHeader.h"
#include "motion.cpp"
#include "lineFollow.cpp"
#include "hand.cpp"
#include "objDetect.cpp"
#include "imageProcessing.cpp"

// names
char motorNames[2][15] = { "left_motor", "right_motor" };
char dsNames[5][15] = { "left_front", "right_front","front_ds","left_back","right_back"};
char irNames[8][4] = { "ir0", "ir1", "ir2", "ir3", "ir4", "ir5", "ir6", "ir7"};
char linearNames[2][15] = { "left_linear", "right_linear"};
char servoName[15] = "Gripper_folder";
char psNames[2][15] = { "left_encoder", "right_encoder" };

// objects
Motor *motors[2];
Motor *linear[2];
Motor *servo;
DistanceSensor* dSensors[5];
DistanceSensor* irPanel[8];
PositionSensor* pSensors[2];
Gyro* gyro;
Camera* camera;
Display* display;


//PID variables
double prevError = 0;
double integral = 0;

//PID variables for object following
double obj_prevError = 0;

//Gripper Lifter
int target_lift=100;

//state variable
int overall_state = 0;

//function init
void angleCorrection (Robot *robot, Motor **motors, DistanceSensor **dSensors);
void wall_pid(Robot* robot, Motor** motors, DistanceSensor** dSensors, PositionSensor** pSensors, int Dir,double target);

//Main
int main(int argc, char **argv) 
{

	Robot *robot = new Robot();
	// init Motors
	for (int i = 0; i < 2; i++)
	{
		motors[i] = robot->getMotor(motorNames[i]);
		motors[i]->setPosition(INFINITY);
		motors[i]->setVelocity(0.0);
	}

	//Hand Motors
	for (int i = 0; i < 2; i++)
	{
		linear[i] = robot->getMotor(linearNames[i]);
		linear[i]->setPosition(0.0);
	}

	servo =  robot->getMotor(servoName);
	servo->setPosition(0.0);

	// init Distance Sensors
	for (int i = 0; i < 5; i++)
	{
		dSensors[i] = robot->getDistanceSensor(dsNames[i]);
		dSensors[i]->enable(TIME_STEP);
	}

	// init IR Panel
	for (int i = 0; i < 8; i++)
	{
		irPanel[i] = robot->getDistanceSensor(irNames[i]);
		irPanel[i]->enable(TIME_STEP);
	}

	// init position sensors
	for (int i=0; i<2; i++){
		pSensors[i] = robot->getPositionSensor(psNames[i]);
		pSensors[i]->enable(TIME_STEP);
	}

	// init gyroscope
	gyro = robot->getGyro("gyro");
	gyro->enable(TIME_STEP);

	//initializing the camera
	camera = robot->getCamera("camera");
	camera->enable(TIME_STEP);

	//initializing the display
	display = robot->getDisplay("display");

	//variables for camera
	int imageWidth = camera->getWidth();
	int imageHeight = camera->getHeight();
	cv::Mat cv_image;
	cv::Mat cv_image_bgr;
	cv::Mat cv_image_hsv;

	// variables for obj coordinates
	double obj_x = -2;
	double obj_y = -2;
	bool arrived = false;

	//detecting colors
	bool arrived_at_wall = false;

	bool break_main_loop = false;
	double front_dis = 1000;
	double rotating_angle = 0;
	double obj_dis_init = 0;
	double obj_dis = 0;
	int object_type1,object_type2;
	int i = 0;
	double KP_wall = 0;
	double const_dis = 0;
	
	//variables
	string IR_Values;
	int current_hand_position = 0; //0--50
	// int target_hand_position = 20;

	bool start_case_3 = true;
	int time;
	int current_time;
	double offset;
	int IR_THRESHOLD = 250; 
	bool first_key_done = false;
	bool sec_key_done = false;
	bool box_done = false;
	bool cylinder_done = false;
	int d_count = 0;
	double hold_val;
	double right_dis = 0;
	bool change_method = false;

	double total_x_gyro_angle = 0;
	bool incline = false;
	double threshold_angle = 18;

	double wall_gyro_total = 0;

	//selecting the RED model or the BLUE mode
	std::ifstream input_file;
	input_file.open("input.txt");

	std::string colour_mode_string;
	std::getline(input_file, colour_mode_string);
	int colour_mode = std::stoi(colour_mode_string); // 0: red and 1: blue

	std::cout << "Colour mode: " << colour_mode << std::endl;

	while (robot->step(TIME_STEP) != -1)
	{
		if (break_main_loop)
		{
			motors[0]->setVelocity(0.0);
			motors[1]->setVelocity(0.0);
			break;
		}
		// XV_print(overall_state)

		switch (overall_state)
		{
		case 0:
			//Line Following Block
			// cout << "Case:0 Line Following" << endl;

			IR_Values = lineFollow::getIRValues(irPanel, IR_THRESHOLD);
			// cout << IR_Values << endl;
			lineFollow::PID(motors, IR_Values, &integral, &prevError);

			if (IR_Values == "00000000"){
				// std::cout << dSensors[0]->getValue() << " & " << dSensors[1]->getValue() << " : " << "Line following sequence is finished" << std::endl;
				overall_state = 1;
				motion::forward(robot, motors, pSensors, dSensors, 150);
				break;
			}

			break;
		
		case 1:
			//Maze navigation
			// cout << "Case:1 Maze Navigation" << endl;

			//Maze navigation
			motion::unit(robot, motors, pSensors, dSensors, gyro, &wall_gyro_total);
			IR_Values = lineFollow::getIRValues(irPanel, IR_THRESHOLD);

			if (IR_Values == "11111111"){
				motors[0]->setVelocity(0.0);
				motors[1]->setVelocity(0.0);

				motion::forward_pid(robot, motors, pSensors, 250);

				// std::cout << "Maze solving sequence finished" << std::endl;
				overall_state = 2;
			}
			break;
		
		case 2:
			// Object Detection and Key Inserting
			// cout << "Case:2 Object Detection and Key Inserting" << endl;

			obj_dis_init = pSensors[0]->getValue();
			arrived = false;
			obj_prevError = 0;
			rotating_angle = 0;
			const_dis = FWD_DISTANCE;

			while (robot->step(TIME_STEP) != -1)  // detecting and grabing the first object
			{
				// cout << "Detecting the object!!" << endl;
				const unsigned char *image = camera->getImage();
				cv::Mat img = imageProcessing::imageToMatrix(image, imageWidth, imageHeight);

				cv::Point2f object_coordinate = imageProcessing::objectTracking(img, imageWidth, imageHeight, OBJECT, display, true);
				obj_x = object_coordinate.x;
				obj_y = object_coordinate.y;
				rotating_angle += gyro->getValues()[1] * TIME_STEP * 0.001;
				// XV_print(rotating_angle)
				obj_dis = pSensors[0]->getValue() - obj_dis_init;

				///////// avoid colliding with the right wall///////////////
				right_dis  = dSensors[1] -> getValue();
				if(right_dis < 300 && !change_method)
				{	
					
					// cout << "change method!!!!" << endl;
					motion::turning(robot, motors, gyro, -rotating_angle);
					motion::forward_pid_slow(robot, motors, pSensors, -obj_dis*35*cos(rotating_angle) + 100); //come to previous position
					motion::turning(robot, motors, gyro, 1.57);
					motion::forward_pid_slow(robot, motors, pSensors, 550);
					motion::turning(robot, motors, gyro, -1.57);
					motion::forward_pid_slow(robot, motors, pSensors, 250); 
					motion::turning(robot, motors, gyro, -1.57/2);
					change_method = true;
					rotating_angle = -1.57/2;  //resetting the rotation angle
				}
				// XV_print(right_dis)

				/////////////////////////////////////////////////////////////
				objDetect::followObject(motors, obj_x, obj_y, &obj_prevError, &arrived);
				if (arrived)
				{
					hand::SetGripperPosition(robot, linear, 50, &current_hand_position); //open the hand
					motion::forward_pid_slow(robot, motors, pSensors, 170);

					hand::SetGripperPosition(robot, linear, 19, &current_hand_position); //close the hand  for ball -10 for box - 20
					// grabed  = true;

					// correct the correction of the oriantation by shaking
					motion::forward_pid(robot, motors, pSensors, -200);
					motors[0] ->setVelocity(NORMAL_SPEED*0.8);
					motors[1] ->setVelocity(NORMAL_SPEED*0.8);
					hand::SetGripperPosition(robot, linear, 40, &current_hand_position);
					hand::SetGripperPosition(robot, linear, 23, &current_hand_position);
					motors[0] ->setVelocity(0);
					motors[1] ->setVelocity(0);
					
					break;
				}
				
			}
			// XV_print(obj_dis_init);
			robot -> step(1500); //important hold for avoid grip fails

			if(!change_method) // for normal method small angles
			{
				if (rotating_angle > 0.3)
				{
					motion::turning(robot, motors, gyro, 3.142 - rotating_angle);
				}
				else
				{
					motion::turning(robot, motors, gyro, 1.57 - rotating_angle);
					motion::forward_pid(robot, motors, pSensors, 250);
					motion::turning(robot, motors, gyro, 1.57);
					const_dis -= 250;
				}

			}
			else // new method
			{
				motion::turning(robot, motors, gyro, 1.57 - rotating_angle);
				motion::forward_pid(robot, motors, pSensors, 250);
				motion::turning(robot, motors, gyro, 1.57);
				
			}
			
			while (robot->step(TIME_STEP) != -1) // go to the wall near yello square
			{	
				// cout << "loop" << endl;
				front_dis = dSensors[2] -> getValue();
				motors[0] ->setVelocity(NORMAL_SPEED*0.8);
				motors[1] ->setVelocity(NORMAL_SPEED*0.8);
				// XV_print(front_dis)

				if (front_dis < 2300)
				{
					motors[0] ->setVelocity(0);
					motors[1] ->setVelocity(0);
					break;					
				}
			}

			motion::turning(robot, motors, gyro, -1.57);
			if (!change_method)
			{
				motion::general_forward(robot, motors, pSensors, const_dis - obj_dis*35*sin(rotating_angle));
			}
			else // new methode forward distance
			{
				motion::general_forward(robot, motors, pSensors, const_dis - 350);
			}

			robot -> step(1000); //important hold for avoid grip fails
			motion::turning(robot, motors, gyro, 1.57);
			robot -> step(1000);
			hand::SetGripperPosition(robot, linear, 26, &current_hand_position); //open the hand
			robot -> step(1000);
			motion::forward_pid(robot, motors, pSensors, -150);

			/// detecting the object///
			i = 0;
			while (robot->step(TIME_STEP) != -1)  // detecting  object
			{
				const unsigned char *image = camera->getImage();
				cv::Mat img = imageProcessing::imageToMatrix(image, imageWidth, imageHeight);
				object_type1 = imageProcessing::detectShape(img, imageWidth, imageHeight, 9, display, true);
				if ( i > 10)
				{
					// std::cout << "Shape Detected: " << object_type1 << std::endl;
					break;	
				}
				i++;
			}

			///////////////////////////
			if(object_type1 == 0) //cylinder
			{
				cout << "cylinder detected" << endl;
				motion::general_forward(robot, motors, pSensors, 210);
				hand::SetGripperPosition(robot, linear, 21, &current_hand_position); //close the grip
				motion::general_forward(robot, motors, pSensors, -100);
				// correcting the distance to the wall
				while (robot->step(TIME_STEP) != -1) // go to the wall near yello square
				{	
					// cout << "loop" << endl;
					front_dis = dSensors[2] -> getValue();
					motors[0] ->setVelocity(NORMAL_SPEED*0.8);
					motors[1] ->setVelocity(NORMAL_SPEED*0.8);
					// XV_print(front_dis)

					if (front_dis < 2300)
					{
						motors[0] ->setVelocity(0);
						motors[1] ->setVelocity(0);
						break;					
					}
				}
				motion::turning(robot, motors, gyro, 3.142);
				motion::general_forward(robot, motors, pSensors, 75);
				motion::turning(robot, motors, gyro, 1.57);

				//go to the key hole
				arrived_at_wall = false;
				while (robot->step(TIME_STEP) != -1 && !arrived_at_wall) // go to the key hole wall 
				{	
					// cout << "loop" << endl;
					front_dis = dSensors[2] -> getValue();
					motors[0] ->setVelocity(NORMAL_SPEED*0.8); //slow down!!!!
					motors[1] ->setVelocity(NORMAL_SPEED*0.8);
					// XV_print(front_dis)
					wall_pid(robot,motors,dSensors,pSensors,'l',3550);

					if (front_dis < 900)
					{
						motors[0] ->setVelocity(0);
						motors[1] ->setVelocity(0);
						// first_wall_passed = true;
						arrived_at_wall = true;
						break;					
					}
				}
				//inserting the square key
				// cout << "inserting the key" <<endl;
				hand::SetGripperPosition(robot, linear, 30, &current_hand_position); //open the hand
				robot -> step(4000);
				motion::general_forward(robot, motors, pSensors, -200); //go backward
				hand::SetGripperPosition(robot, linear, 12, &current_hand_position); //close the hand
				motion::general_forward(robot, motors, pSensors, 215);
				robot -> step(1000); //to slow down the robot
				motion::general_forward(robot, motors, pSensors, -500); //go backward
				cylinder_done =true;

			}
			
			else if (object_type1 == 1) //box
			{
				motion::turning(robot, motors, gyro, -1.57);
				motion::forward_pid(robot, motors, pSensors, 320);
				motion::turning(robot, motors, gyro, 1.57);
				motion::forward_pid(robot, motors, pSensors, 250);
				motion::turning(robot, motors, gyro, 1.57);
				/// detecting the object///

				i = 0;
				while (robot->step(TIME_STEP) != -1)  // detecting  object
				{
					const unsigned char *image = camera->getImage();
					cv::Mat img = imageProcessing::imageToMatrix(image, imageWidth, imageHeight);
					object_type2 = imageProcessing::detectShape(img, imageWidth, imageHeight, 9, display, true);
					if ( i > 10)
					{
						// std::cout << "Shape Detected: " << object_type2 << std::endl;
						break;	
					}
					i++;
				}

				///////////////////////////////////////

				if (object_type2 == 0) //cylinder
				{
					cout << "cylinder detected" << endl;
					hand::SetGripperPosition(robot, linear, 50, &current_hand_position); //open the hand

					obj_dis_init = pSensors[0]->getValue();
					arrived = false;
					obj_prevError = 0;
					rotating_angle = 0;
					const_dis = FWD_DISTANCE;

					while (robot->step(TIME_STEP) != -1)  // detecting and grabing the cylinder
					{
						// cout << "Detecting the object!!------------------------p" << endl;
						const unsigned char *image = camera->getImage();
						cv::Mat img = imageProcessing::imageToMatrix(image, imageWidth, imageHeight);

						cv::Point2f object_coordinate = imageProcessing::objectTrackingLeft(img, imageWidth, imageHeight, OBJECT, display, true);
						obj_x = object_coordinate.x;
						obj_y = object_coordinate.y;

						rotating_angle += gyro->getValues()[1] * TIME_STEP * 0.001;
						// XV_print(rotating_angle)
						obj_dis = pSensors[0]->getValue() - obj_dis_init;
						objDetect::followObject(motors, obj_x, obj_y, &obj_prevError, &arrived);
						if (arrived)
						{
							hand::SetGripperPosition(robot, linear, 50, &current_hand_position); //open the hand
							motion::forward_pid(robot, motors, pSensors, 165);

							hand::SetGripperPosition(robot, linear, 19, &current_hand_position); //close the hand  for ball -10 for box - 20

							// correct the correction of the oriantation by shaking
							motion::forward_pid(robot, motors, pSensors, -200);
							motors[0] ->setVelocity(NORMAL_SPEED);
							motors[1] ->setVelocity(NORMAL_SPEED);
							hand::SetGripperPosition(robot, linear, 40, &current_hand_position);
							hand::SetGripperPosition(robot, linear, 23, &current_hand_position);
							motors[0] ->setVelocity(0);
							motors[1] ->setVelocity(0);
							
							break;
						}
						
					}

					////////////////////
					robot -> step (1000); // important delay to avoid gripper fails
					motion::turning(robot, motors, gyro, 1.57- rotating_angle); //correcting and rotate 90 after grabing cylinder
					motion::general_forward(robot, motors, pSensors, 350);
					motion::turning(robot, motors, gyro, 3.142);

					while (robot->step(TIME_STEP) != -1) // go to the wall near yello square
					{	
						// cout << "loop" << endl;
						front_dis = dSensors[2] -> getValue();
						KP_wall = front_dis/4000;
						motors[0] ->setVelocity(NORMAL_SPEED*0.8*KP_wall);
						motors[1] ->setVelocity(NORMAL_SPEED*0.8*KP_wall);
						// XV_print(front_dis)

						if (front_dis < 2300)
						{
							motors[0] ->setVelocity(0);
							motors[1] ->setVelocity(0);
							break;					
						}
					}

					motion::forward_pid(robot, motors, pSensors, -100);
					motion::turning(robot, motors, gyro, -1.57);

					//go to the key hole
					while (robot->step(TIME_STEP) != -1) // go to the wall near yello square
					{	
						// cout << "loop" << endl;
						front_dis = dSensors[2] -> getValue();
						KP_wall = front_dis/4000;
						motors[0] ->setVelocity(NORMAL_SPEED*0.8*KP_wall);
						motors[1] ->setVelocity(NORMAL_SPEED*0.8*KP_wall);
						// XV_print(front_dis)
						wall_pid(robot,motors,dSensors,pSensors,'l',3550);
						if (front_dis < 900)
						{
							motors[0] ->setVelocity(0);
							motors[1] ->setVelocity(0);
							break;					
						}
					}
					//inserting the square key
					// cout << "inserting the key" <<endl;
					hand::SetGripperPosition(robot, linear, 30, &current_hand_position); //open the hand
					robot -> step(4000);
					motion::general_forward(robot, motors, pSensors, -200); //go backward
					hand::SetGripperPosition(robot, linear, 12, &current_hand_position); //close the hand
					// hand::liftHand(servo,robot, -1,20); //low the hand
					motion::general_forward(robot, motors, pSensors, 215);
					robot -> step(1000); //to slow down the robot
					motion::general_forward(robot, motors, pSensors, -500); //go backward
					cylinder_done = true;
					

				}
				else if (object_type2 == 1) //box
				{
					cout << "box detected" << endl;

					hand::SetGripperPosition(robot, linear, 50, &current_hand_position); //open the hand
					motion::forward_pid(robot, motors, pSensors, 200);
					hand::SetGripperPosition(robot, linear, 21, &current_hand_position); //close the grip
					robot -> step(1000); //important hold for avoid grip fails
					motion::turning(robot, motors, gyro, 1.57);
					motion::general_forward(robot, motors, pSensors, 350);
					motion::turning(robot, motors, gyro, 3.142);

					while (robot->step(TIME_STEP) != -1) // go to the wall near yello square
					{	
						// cout << "loop" << endl;
						front_dis = dSensors[2] -> getValue();
						KP_wall = front_dis/4000;
						motors[0] ->setVelocity(NORMAL_SPEED*0.8*KP_wall);
						motors[1] ->setVelocity(NORMAL_SPEED*0.8*KP_wall);
						// XV_print(front_dis)

						if (front_dis < 1500)
						{
							motors[0] ->setVelocity(0);
							motors[1] ->setVelocity(0);
							break;					
						}
					}

					motion::turning(robot, motors, gyro, -1.55);
					
					//go to the key hole
					while (robot->step(TIME_STEP) != -1) 
					{	
						// cout << "loop" << endl;
						front_dis = dSensors[2] -> getValue();
						KP_wall = front_dis/4000;
						motors[0] ->setVelocity(NORMAL_SPEED*0.8*KP_wall);
						motors[1] ->setVelocity(NORMAL_SPEED*0.8*KP_wall);
						// XV_print(front_dis)
						wall_pid(robot,motors,dSensors,pSensors,'l',1540);
						if (front_dis < 1000)
						{
							motors[0] ->setVelocity(0);
							motors[1] ->setVelocity(0);
							break;					
						}
					}
					//inserting the square key
					// cout << "inserting the key" <<endl;
					hand::SetGripperPosition(robot, linear, 30, &current_hand_position); //open the hand
					robot -> step(4000);
					motion::general_forward(robot, motors, pSensors, -200); //go backward
					hand::SetGripperPosition(robot, linear, 12, &current_hand_position); //close the hand
					motion::forward_pid(robot, motors, pSensors, 230);
					robot -> step(1000); //to slow down the robot
					motion::general_forward(robot, motors, pSensors, -500); //go backward
					box_done = true;
				}
				else  // cannot detect
				{
					cout << "object cannot detect" << endl;

				}
			}
			else // cannot detect
			{
				cout << "object cannot detect" << endl;

			}

			/////////////terminate logic ///////////////////////////////
			
			if ( (box_done || cylinder_done) && !first_key_done)
			{

				first_key_done = true;
				// cout << "going for the secound object" << endl;

				//go to begining
				motion::turning(robot, motors, gyro, 1.57);
				while (robot->step(TIME_STEP) != -1) // go to the wall near yello square
				{	
					// cout << "loop" << endl;
					front_dis = dSensors[2] -> getValue();
					KP_wall = front_dis/4000;
					motors[0] ->setVelocity(NORMAL_SPEED*0.8*KP_wall);
					motors[1] ->setVelocity(NORMAL_SPEED*0.8*KP_wall);

					if (front_dis < 1500) //min gap
					{
						motors[0] ->setVelocity(0);
						motors[1] ->setVelocity(0);
						break;					
					}
				}
				motion::turning(robot, motors, gyro, 1.57);
				while (robot->step(TIME_STEP) != -1) // go to the begining - wall following
				{	
					// cout << "loop" << endl;
					front_dis = dSensors[2] -> getValue();
					motors[0] ->setVelocity(NORMAL_SPEED*0.8); //slow down!!!!
					motors[1] ->setVelocity(NORMAL_SPEED*0.8);
					// XV_print(front_dis)
					wall_pid(robot,motors,dSensors,pSensors,'r',1500);

					if (front_dis < 4000)
					{
						motors[0] ->setVelocity(0);
						motors[1] ->setVelocity(0);
						// first_wall_passed = true;
						arrived_at_wall = true;
						break;					
					}
				}
				motion::forward_pid(robot, motors, pSensors, 200);
				motion::turning(robot, motors, gyro, 1.57);

			}
			else if (first_key_done && !sec_key_done) //all keys complete
			{
				// cout << "sec_key_done" << endl;
				sec_key_done = true;
				//come back and grab the ball
				motion::turning(robot, motors, gyro, -1.57);

				obj_dis_init = pSensors[0]->getValue();
				arrived = false;
				obj_prevError = 0;
				rotating_angle = 0;
				const_dis = FWD_DISTANCE;
				while (robot->step(TIME_STEP) != -1)  // detecting and grabing the colour ball
				{
					// cout << "Detecting the object!!" << endl;
					const unsigned char *image = camera->getImage();
					cv::Mat img = imageProcessing::imageToMatrix(image, imageWidth, imageHeight);

					cv::Point2f object_coordinate = imageProcessing::objectTracking(img, imageWidth, imageHeight, 3 + colour_mode, display, true);
					obj_x = object_coordinate.x;
					obj_y = object_coordinate.y;

					rotating_angle += gyro->getValues()[1] * TIME_STEP * 0.001;
					// XV_print(rotating_angle)
					obj_dis = pSensors[0]->getValue() - obj_dis_init;
					objDetect::followObject(motors, obj_x, obj_y, &obj_prevError, &arrived);
					if (arrived)
					{
						hand::SetGripperPosition(robot, linear, 50, &current_hand_position); //open the hand
						motion::forward_pid(robot, motors, pSensors,135);
						hand::SetGripperPosition(robot, linear, 19, &current_hand_position); //close the hand  for ball -10 for box - 20
						// grabed  = true;						
						break;
					}
					
				}
				// XV_print(obj_dis_init);
				robot -> step(1500); //important hold for avoid grip fails

					motion::turning(robot, motors, gyro, 3.142 - rotating_angle);
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

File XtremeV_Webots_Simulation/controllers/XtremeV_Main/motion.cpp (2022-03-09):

#include "MainHeader.h"

void motion::init_turn(Motor** motors, double angle){
    motion::turn_flag = true;
    motion::angle_error = angle;
    motion::prev_angle_error = angle;
    motion::integral_rotate = 0;

    motion::start_motors(motors, MAX_SPEED, 0);
}

void motion::turn(Motor** motors, Gyro* gyro){
    motion::angle_error -= gyro->getValues()[1] * TIME_STEP * 0.001;
    motion::integral_rotate += motion::angle_error;

    double motor_speed = motion::KP_rotate * motion::angle_error + motion::KI_rotate * motion::integral_rotate + motion::KD_rotate * (motion::angle_error - motion::prev_angle_error);

    motion::prev_angle_error = motion::angle_error;

    if (std::abs(motor_speed) >= std::abs(MAX_SPEED)){
      motor_speed = MAX_SPEED * motor_speed / std::abs(motor_speed);
    }

    motion::start_motors(motors, motor_speed, 2);

    if(std::abs(motion::angle_error) <= 0.01){
        motion::turn_flag = false;
        motion::integral_rotate = 0;
        motion::stop_motors(motors);
    }

    // std::cout << "Rotated angle error: " << angle_error << std::endl;
}

void motion::start_motors(Motor** motors, double speed, int mode){
  // std::cout << speed << std::endl;

  //straight
  if (mode == 0){
    for (int i=0; i<2; i++){
      motors[i]->setVelocity(speed);
    }
  }
  //right turn
  else if(mode == 1){
    motors[0]->setVelocity(speed);
    motors[1]->setVelocity(-speed);
  }
  //left turn
  else if(mode == 2){
    motors[0]->setVelocity(-speed);
    motors[1]->setVelocity(speed);
  }
}

void motion::stop_motors(Motor** motors){
  for (int i=0; i<2; i++){
    motors[i]->setVelocity(0.0);
  }
}

double motion::increase_speed(double ref_speed, double offset){
  return std::min( std::max( ref_speed + offset, -1*(double)MAX_SPEED ), (double)MAX_SPEED );
}

void motion::forward(Robot* robot, Motor** motors, PositionSensor** pSensors, DistanceSensor** dSensors, int distance)
{
  double lambda = distance/35;
  double ang=pSensors[0] -> getValue();
  double ang1=ang;
  // cout<<ang1<<endl;
  while (robot->step(TIME_STEP) != -1)
  {
    //cout<<ang1<<endl;
    ang1=pSensors[0] -> getValue();
    // cout<<ang1<<endl;
    if (ang1-ang>lambda)////-//////////////////////[12.5 change kranw]
    {
      for(int k=0;k<2;k++)
      {
        motors[k]->setVelocity(0);
      }
      return;
    }
      for(int k=0;k<2;k++)
      {
        motors[k]->setVelocity(MAX_SPEED);
      }
  }
}

void motion::stop(Motor** motors)
{
  for(int k=0;k<2;k++)
  {
    motors[k]->setVelocity(0);
  }
}

bool motion::is_wall(DistanceSensor** dSensors, char x)
{
  if (x=='l')
  {
    if (dSensors[0]->getValue()<4000)
    {
      return true;
    }
    return false;
  }
  else if (x=='f')
  {
    if (dSensors[2]->getValue()<4000)
    {
      return true;
    }
    return false;
  }
  else
  {
    if (dSensors[1]->getValue()<4000)
    {
      return true;
    }
    return false;
  }
}

void motion::turning(Robot* robot, Motor** motors, Gyro* gyro, double angle){
	motion::init_turn(motors, angle);
	while(robot->step(TIME_STEP) != -1){
		if (motion::turn_flag){
			motion::turn(motors, gyro);
		}
		else{
			break;
		}
	}
}

int motion::Wall_Follower(Robot* robot, Motor** motors, DistanceSensor** dSensors, Gyro* gyro, PositionSensor** pSensors, double wall_prev_val, double* wall_gyro_total){
  double distances[5];
  for(int j=0;j<5;j++)
  {
    distances[j]=dSensors[j]->getValue();
  }

  double center_err=distances[0]-900;
  // double align_err=distances[1]-distances[4];
  double velocity_err;

  *wall_gyro_total += gyro->getValues()[1] * TIME_STEP * 0.001;

  // std::cout << "Gyro Value: " << *wall_gyro_total << std::endl;

  if (wall_prev_val == NULL){
    velocity_err=motion::kp1*center_err;
  }
  else{
    velocity_err = motion::kp1 * center_err + motion::kd1 * (center_err - wall_prev_val);
  }

  double Left_V=NORMAL_SPEED-velocity_err;
  double Right_V=NORMAL_SPEED+velocity_err;

  // std::cout << "Current motor speed: " << motors[0]->getVelocity() << " " << motors[1]->getVelocity() << std::endl;
  // std::cout << "Distance sensor values: " << dSensors[0]->getValue() << " " << dSensors[1]->getValue() << " " << dSensors[2]->getValue() << std::endl;
  // std::cout << "Next motor speed: " << std::max(std::min(double(MAX_SPEED),Left_V),double(-MAX_SPEED)) << " " << std::max(std::min(double(MAX_SPEED),Right_V),double(-MAX_SPEED)) << std::endl;

  //std::cout << center_err<<endl;//std::max(std::min(float(MAX_SPEED),Left_V),float(-MAX_SPEED))<<"  "<< std::max(std::min(float(MAX_SPEED),Right_V),float(-MAX_SPEED)) <<endl;
  if (distances[1]>2500 || distances[0]>2500 || distances[2]<1500)
  {
    motion::turning(robot, motors, gyro, -1*(*wall_gyro_total));
    *wall_gyro_total = 0;

    if (distances[2]<3000)
    {
      if(distances[0]>distances[1])
      {
      motion::turning(robot, motors, gyro, -180 * 3.14/180);
      return 1;
      }
      else
      {
      motion::turning(robot, motors, gyro, -180 * 3.14/180);
      return 1;
      }
      
    }
    motion::forward(robot, motors, pSensors, dSensors, motion::d);
    // std::cout << distances[0]<< " 2Wall "<<distances[1]<<endl;
    return 0;
  }

  motors[0]->setVelocity(std::max(std::min(double(MAX_SPEED),Left_V),double(-MAX_SPEED)));
  motors[1]->setVelocity(std::max(std::min(double(MAX_SPEED),Right_V),double(-MAX_SPEED)));

  wall_prev_val = center_err;

  return 2;
}

int motion::One_Wall_Follow(Robot* robot, Motor** motors, DistanceSensor** dSensors, PositionSensor** pSensors, char Dir)
{
  int i=0;
  int mark=1;  
  double distances[5];
  for(int j=0;j<5;j++)
  {
    distances[j]=dSensors[j]->getValue();
  }
  if (Dir=='l')
  {
    i=1;
    mark=-1;
  }
  double align_err=distances[1-i]-distances[4-i];
  float velocity_err=motion::kp2*align_err;
  float Left_V=NORMAL_SPEED+mark*velocity_err;
  float Right_V=NORMAL_SPEED-mark*velocity_err;
    
  motors[0]->setVelocity(std::max(std::min(float(MAX_SPEED),Left_V),float(-MAX_SPEED)));
  motors[1]->setVelocity(std::max(std::min(float(MAX_SPEED),Right_V),float(-MAX_SPEED)));
  if (distances[i]<2500)
  {
    //std::cout << " exit "<<endl;
    motion::forward(robot, motors, pSensors, dSensors, motion::d);
    // std::cout << distances[0]<< " 1Wall "<<distances[1]<<endl;
    return 0;
  }
  return 3+i;
}

int motion::No_Wall_Follow(Robot* robot, Motor** motors, DistanceSensor** dSensors, PositionSensor** pSensors)
{
  double distances[5];
  for(int j=0;j<5;j++)
  {
    distances[j]=dSensors[j]->getValue();
  }
  motors[0]->setVelocity(MAX_SPEED);
  motors[1]->setVelocity(MAX_SPEED);
  if (distances[0]<2500 || distances[1]<2500)
  {
    //std::cout << " exit "<<endl;
    motion::forward(robot, motors, pSensors, dSensors, motion::d);
    // std::cout << distances[0]<< " 0Wall "<<distances[1]<<endl;
    return 0;
  }
  return 5;
}
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

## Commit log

2022-02-12 added the test script used for creating the wheel encoder functionality
2022-02-12 add the PID left rotation
2022-02-13 add namespace for PID turning
2022-02-13 add SolidWorks part
    [last pathnew2.STL]
2022-02-13 add new dotted line path model
    [last pathnew.STL]
2022-02-16 Added the maze controller and 2 more d sensors
2022-02-16 gripper in main
2022-03-09 update the finalized files
    [25D-metal-gearmotor-75-encoder.SLDPRT, Assem1.SLDASM, Balle.SLDPRT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]
